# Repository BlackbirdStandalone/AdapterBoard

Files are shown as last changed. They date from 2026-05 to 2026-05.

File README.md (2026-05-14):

# Honda CBR1100XX Super Blackbird - Wiring harness adapter board

This project incorporates a printed circuit board design that allows you to connect from the OEM Honda CBR1100XX Blackbird wiring harness to your stand-alone ECU of choice.
This adapter board specifically targets the early 2000's model EFI Honda Blackbird.

In my case, it is an Australian 2002 model.

The OEM Keihin ECU contains two groups of 22 connector pins that mate with bikes wiring harness. The harness side contains the two connectors (black and light gray) that the ECU mates with. These 22-pin connectors are proprietary and are located underneath the seat at the rear of the motorcycle.

This PCB design provides a means of conveniently interfacing with the existing 22-pin connector to your specific standalone ECU of choice without having to sever the existing wiring harness.
A custom wiring harness can then be separately built to interface to the stand alone ECU via standard Molex connectors numbered at the top of the board.<br/> The benefit of such an interface board also allows you to revert to the original Keihin ECU if you so wish since it allows the bikes wiring harness to remain undisturbed.</BR>
Note: This will only be the case if the camshaft 3-tooth trigger wheel is also left undisturbed.

Fitment to a motorcycle will require the construction of two PCB's. An example of two completed boards are shown below together with its fitment to the existing wiring harness in place of the Keihin ECU.

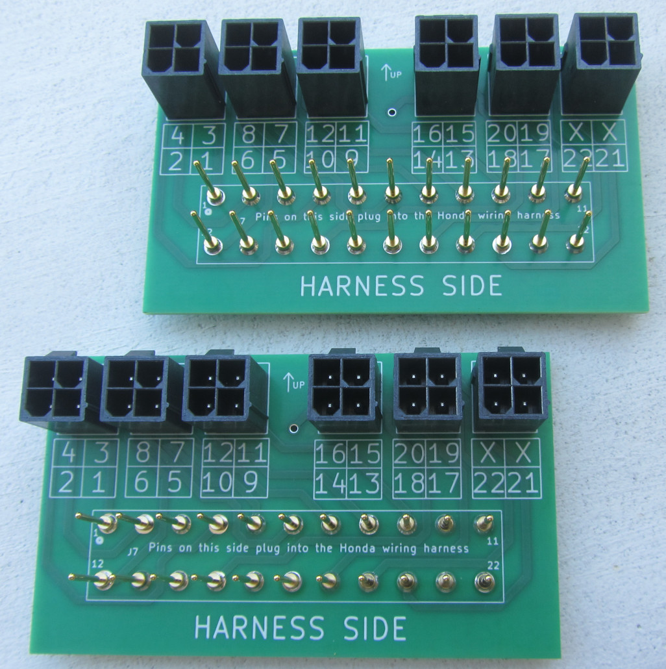
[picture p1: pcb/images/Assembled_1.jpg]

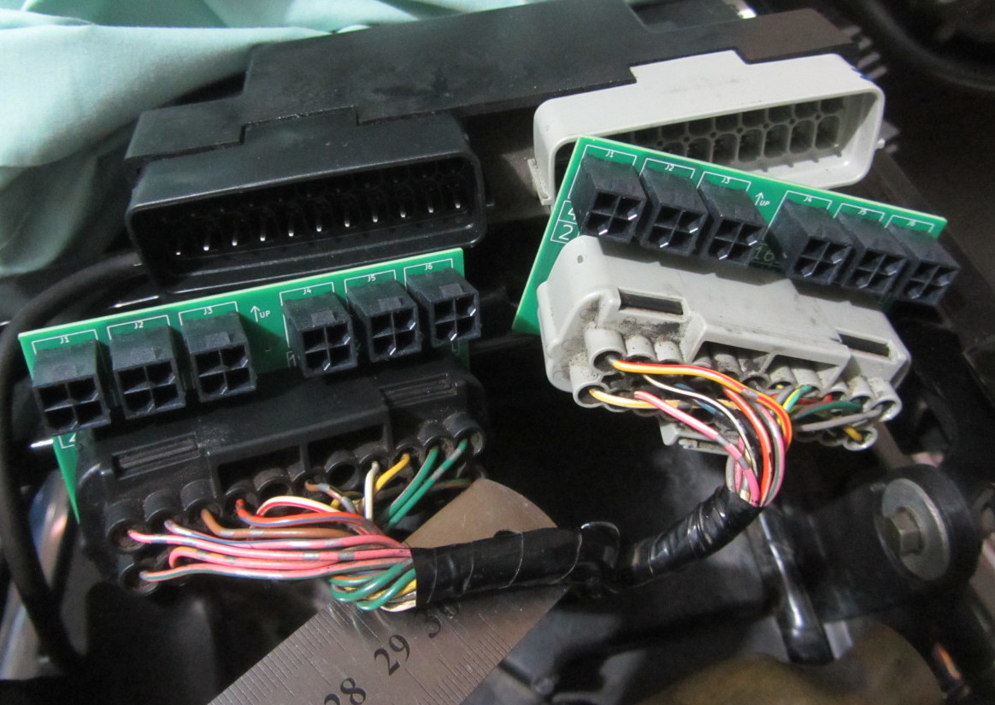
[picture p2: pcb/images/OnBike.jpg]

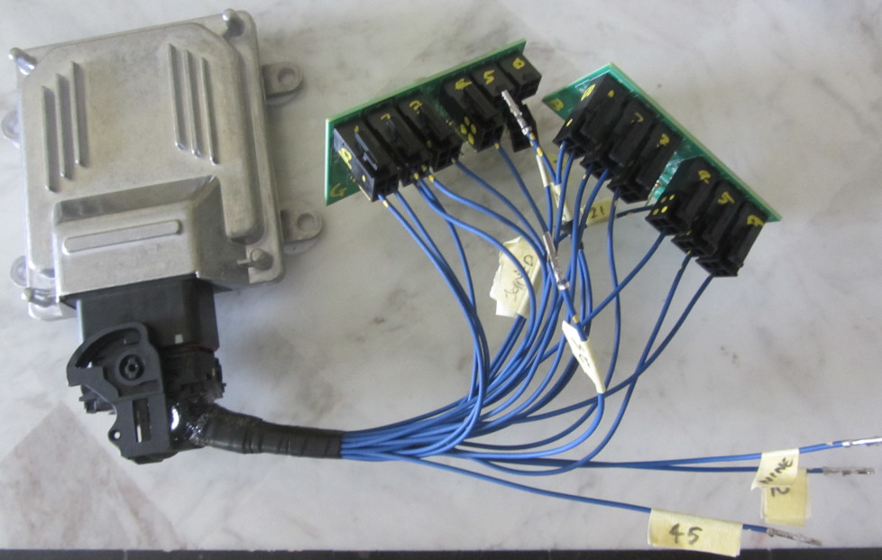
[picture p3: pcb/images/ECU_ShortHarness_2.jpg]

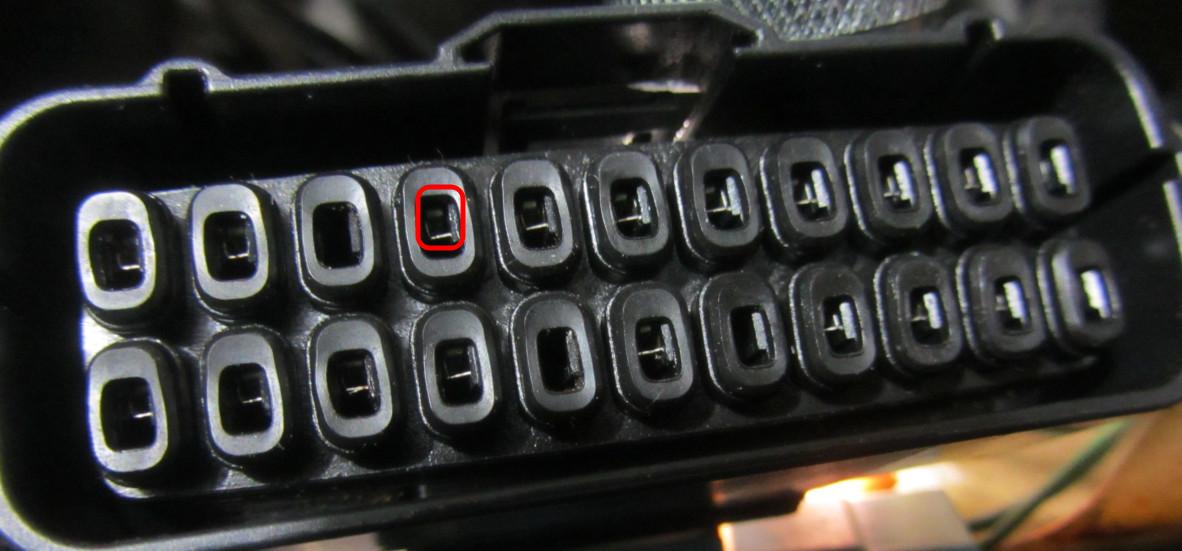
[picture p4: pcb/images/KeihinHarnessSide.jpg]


Note: This project is in its early stages, so does not discuss packaging or sealing of the boards from the elements at this stage. It is evolutionary in nature and will attempt to improve shortcomings over time as new ideas come to light.

</BR>

### Extra Notes
As of this current version (v0.2b), the 22 x round gold-plated pin connectors on the lower half of the board are the closest match I could find as a replacement to the stock Keihin pins.</br>
The stock Keihin pins are 1.0mm wide and 0.7mm tall, therefore a rectangular pin. The replacement I have used is a 1.0mm round style pin. It fits into the harness side very snug. The search for a perfect pin match will continue for future boards revisions.

The last picture displays the Honda/Keihin side of the main bikes wiring harness. It is important that the receptacle (receiver side) is correctly mated with the pins on the PCB since it is easy to mis-align. The area of entry is shown in red. Therefore care must be taken with the pin alignment as the boards are plugged into the black and gray harness side connectors on the bike. The connection will be on the tight side due to the 1.0mm round pins, but they will work.

The pin spacings on the Keihin 22-way connector are 8.5mm in the vertical and 5.8mm horizontally.

The upper half of the board contains a series of 6 x 4-way Molex connectors. The connectors are part of the 'Mini Fit Jnr' family of Molex connectors. The example shown above uses automotive 20 AWG wire. The choice to use many smaller connectors rather than a single 24 way connector was mainly due to stock availability. The 4-way connectors are very common.

</BR>

### Project Details

<table border="1">

<tr> 
<td width="20%">
<strong><u>Current Revision</u></strong>
</td>
<td width="60%">
<strong><u>Date</u></strong>
</td>
<td width="20%">
<strong><u>Author</u></strong>
</td>
</tr>

<tr>
<td width="20%">
v0.2b
</td>
<td width="60%">
May 2026
</td>
<td width="20%">
Alex Kiaos
</td>
</tr>

</table>

</BR>

This project has been designed in Kicad 6.0.11 under linux and is licenced under the CERN Open Hardware Licence Version 2 - Strongly Reciprocal (CERN-OHL-S).</br></br>

The directory structure of this project is as follows:

<p id=directories>
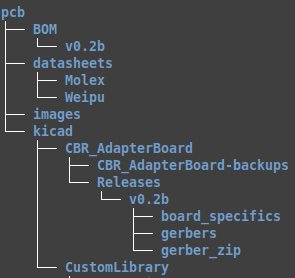
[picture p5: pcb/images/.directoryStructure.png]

</p>

<table border="1">

<tr> 
<td width="20%">
<strong><u>Directory</u></strong>
</td>
<td width="80%">
<strong><u>Description</u></strong>
</td>

</tr>

<tr>
<td width="20%">
BOM
</td>
<td width="80%">
Bill of materials
</td>
</tr>

<tr>
<td width="20%">
datasheets
</td>
<td width="80%">
Data sheets for pins and connectors
</td>
</tr>

<tr>
<td width="20%">
images
</td>
<td width="80%">
Various images, pictures, board renditions
</td>
</tr>

<tr>
<td width="20%">
kicad
</td>
<td width="80%">
The main kicad project folder.<br>
This contains the project itself (uses kicad 6.0.11)</br>
The main project file is 'CBR_AdapterBoard.kicad_pro' found under</br>'/pcb/kicad/CBR_AdapterBoard'.</br></br>
Gerber files can be found as a group of 9 individual files under the 'gerbers' folder or as a single zipped file under the 'gerber_zipped' folder for uploading to a PCB house for manufacture.</br></br>
The 'CustomLibrary' folder contains the custom symbols and footprints used in the project.
</td>

</table>

</br>

After cloning the repository and opening the project for the first time, you may need to set up the symbol and footprint library paths.

To setup the symbols library, in the menu:<br>
<pre><i>Preferences -> Manage Symbol Libraries</i><br>
  Then in the 2nd tab under 'Project specific libraries' add the following:<br>
Nickname: <b>Blackbird</b><br>
Library Path: <b>${KIPRJMOD}/../CustomLibrary/symbols/Blackbird_symbols.kicad_sym</b><br>
</pre>
<br><br>

To setup the footprint library, in the menu:<br>
<pre><i>Preferences -> Manage Footprint Libraries</i><br>
  Then in the 2nd tab under 'Project specific libraries' add the following<br>
Nickname: <b>Blackbird</b><br>
Library Path: <b>${KIPRJMOD}/../CustomLibrary/footprints/</b><br>
</pre>
<br>

# Relevant links

### PCBWay
To visit the PCBWay project and/or place an [order](https://www.pcbway.com/project/shareproject/Honda_CBR1100XX_Super_Blackbird_ECU_adapter_board_for_a_standalone_ECU_a730cd35.html).

### Wiring Harness & Pinouts
To see the ECU pin-out details, refer to the latest pdf file at:
[Wiring Harness Pinout diagram](https://github.com/BlackbirdStandalone/Documentation/tree/main/wiring).

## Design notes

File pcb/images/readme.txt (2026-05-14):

This folder contains various pictures & board renditions related to this adapter board.

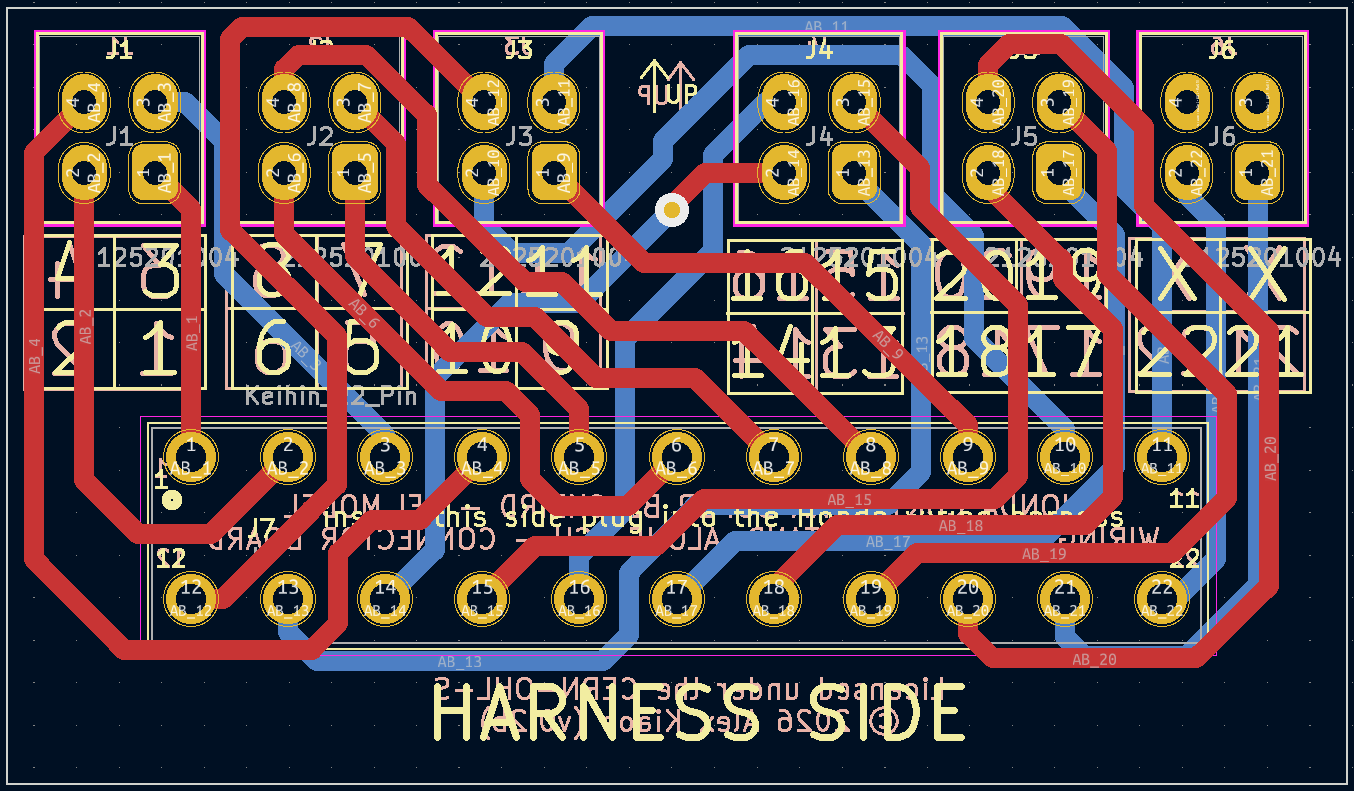
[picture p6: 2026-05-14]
pcb/kicad/CBR_AdapterBoard/Releases/v0.2b/board_specifics/PcbLayout.png

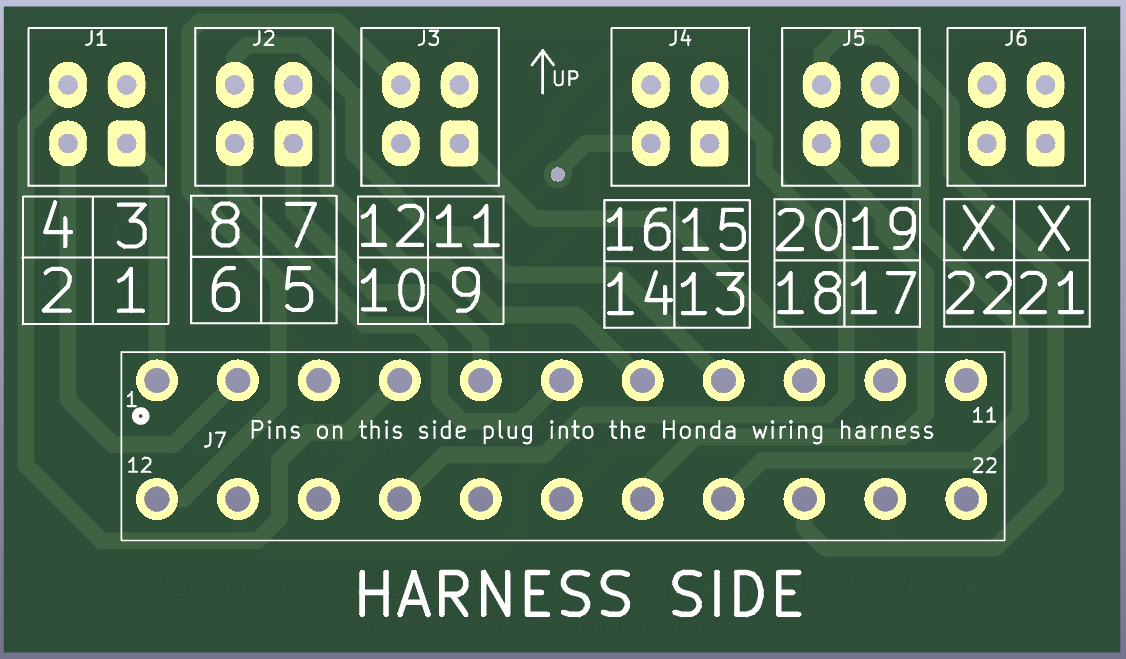
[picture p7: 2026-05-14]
pcb/kicad/CBR_AdapterBoard/Releases/v0.2b/board_specifics/TopSide.png

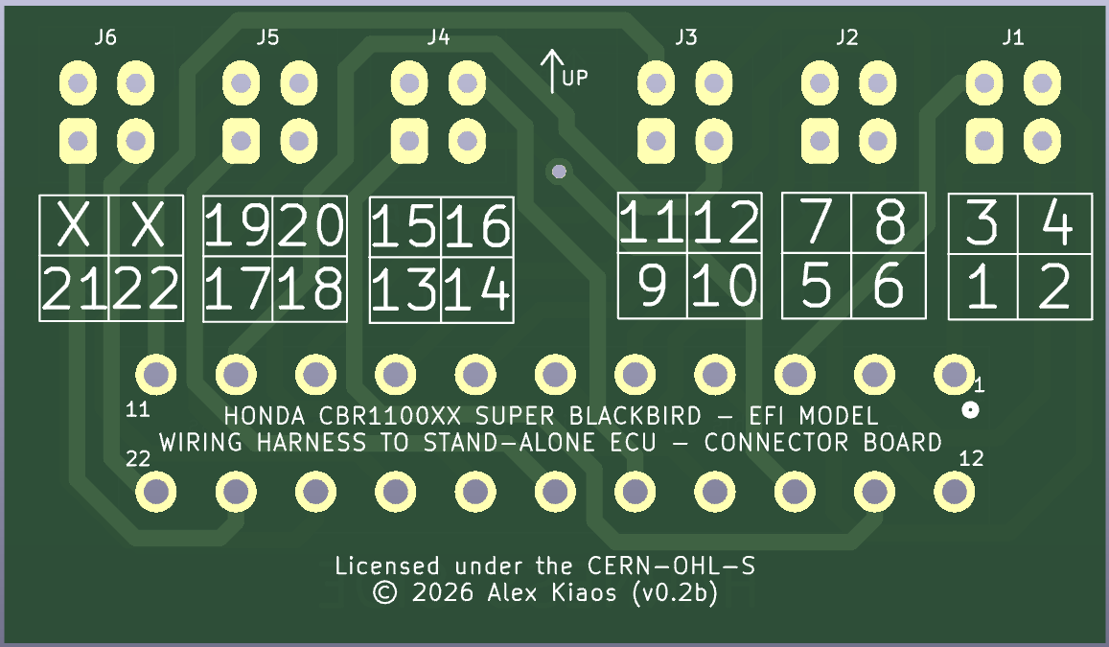
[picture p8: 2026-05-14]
pcb/kicad/CBR_AdapterBoard/Releases/v0.2b/board_specifics/BottomSide.png

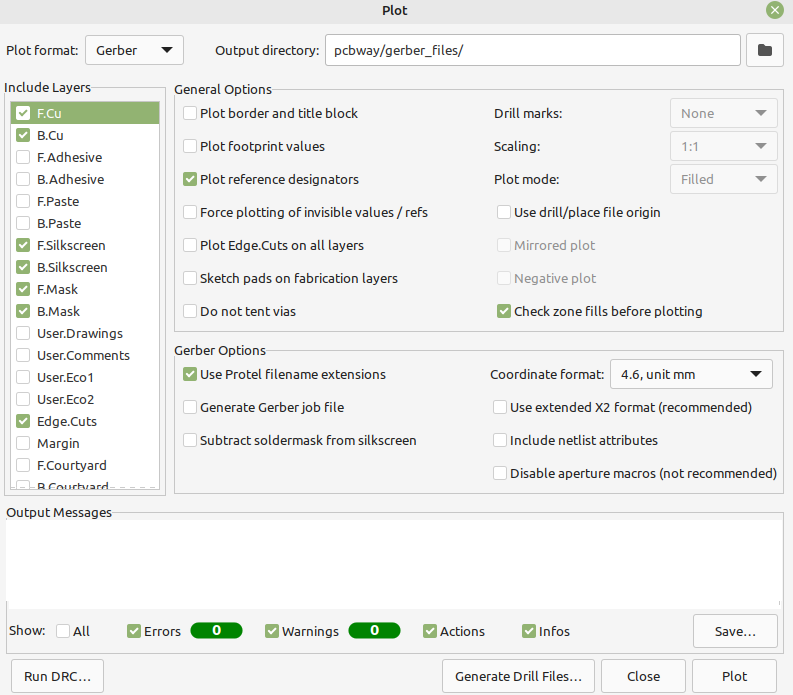
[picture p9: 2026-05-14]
pcb/kicad/CBR_AdapterBoard/Releases/v0.2b/board_specifics/Pcbway_gerber_config.png

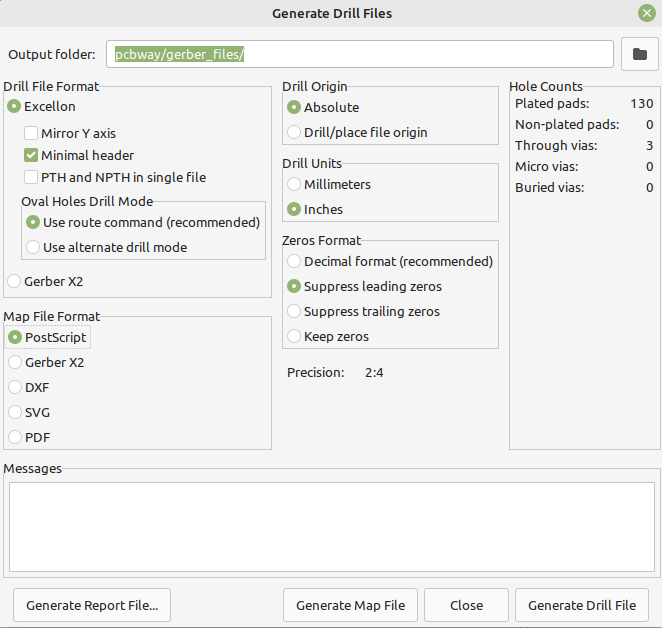
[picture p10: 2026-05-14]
pcb/kicad/CBR_AdapterBoard/Releases/v0.2b/board_specifics/Pcbway_drill_config.png

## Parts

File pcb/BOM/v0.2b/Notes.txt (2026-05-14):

BILL OF MATERIALS (BOM)
----------------------

For one motorcycle, you will need the following parts:

- 2 x PCB boards

- 12 x 4 way Molex connectors (Plug) - Digikey part No: 0462071004-ND
- 12 x 4 way Molex connectors (Receptacle) - Digikey part No: WM13487-ND

- 44 x rectangular connectors - Digikey part No: 0039000038 (order more in case spares are needed)

- 44 x pins - Digikey part No: 5040-YJ1-17-0.52AU-ND (order more in case spares are needed)

Details are outlined in the spreadsheet found in this folder.

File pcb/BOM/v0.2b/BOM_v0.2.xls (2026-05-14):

Category On Board | Board Reference | OEM PART | DigiKey Part No | Series | Description | Link
Pins to Honda harness | J7 | YJ1-17-0.52AU | 5040-YJ1-17-0.52AU-ND | - | Pin Contact 20-24 AWG Size 1.0mm Crimp Gold | https://mm.digikey.com/Volume0/opasdata/d220001/medias/docus/8456/Crimp%20contact%20and%20tool.pdf
PLUG (Molex) | J1-J6 | 462071004 (MOLEX) | 0462071004-ND | Mini-Fit Jr. 46207 Series | CONN HEADER VERT 4POS 4.2MM | https://www.digikey.com.au/en/products/detail/molex/0462071004/3311552
PLUG (Receptacle) | J1-J6 | 39013045 (MOLEX) | WM13487-ND | 5557 | CONN RCPT HSG 4POS 4.20MM | https://www.digikey.com.au/en/products/detail/molex/0039013045/3160117
WIRING - (Wire to receptacle) | J1-J6 | 39000038 (MOLEX) | WM2501TR-ND or WM2501CT-ND | Mini-Fit Jr 5556 | CONN SOCKET 18-24AWG CRIMP TIN | https://www.digikey.com.au/en/products/detail/molex/0039000038/413211
(alternate) WIRING - (Wire to receptacle) |  | 39000073 (MOLEX) | WM6890TR-ND or WM6890CT-ND | Mini-Fit Jr 5556 | CONN SOCKET 18-24AWG CRIMP GOLD | https://www.digikey.com.au/en/products/detail/molex/0039000073/3044236
Notes
TO ORDER IN GREEN

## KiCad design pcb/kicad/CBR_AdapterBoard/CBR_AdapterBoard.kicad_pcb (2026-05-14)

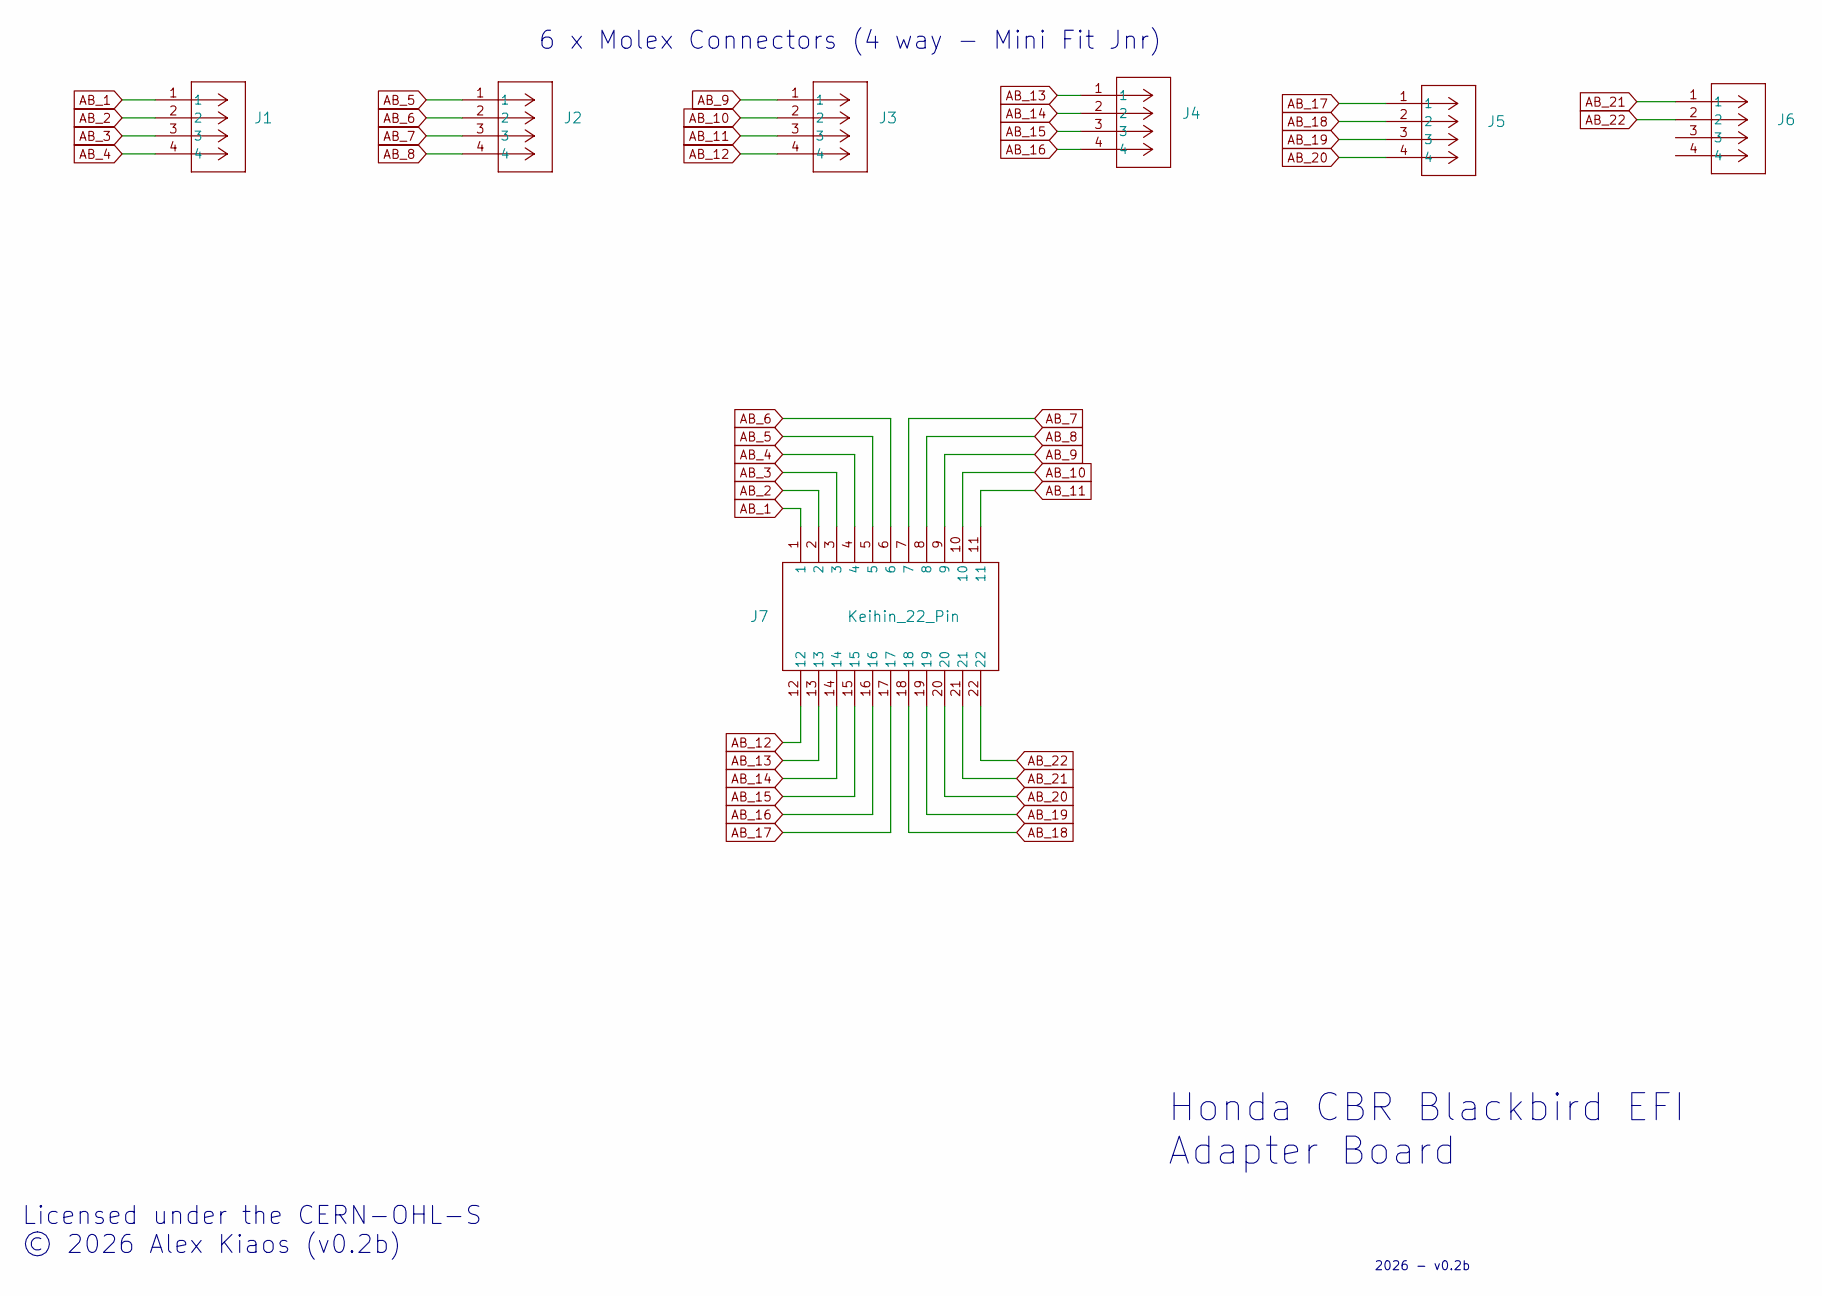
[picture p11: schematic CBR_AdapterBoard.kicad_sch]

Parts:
J1, J2, J3, J4, J5, J6: 2125201004; 4-Way-Molex_Connector-MiniFit-JNR
J7: Keihin_22_Pin; Blackbird_22_pin_keihin

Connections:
AB_1: J1.1, J7.1
AB_2: J1.2, J7.2
AB_3: J1.3, J7.3
AB_4: J1.4, J7.4
AB_5: J2.1, J7.5
AB_6: J2.2, J7.6
AB_7: J2.3, J7.7
AB_8: J2.4, J7.8
AB_9: J3.1, J7.9
AB_10: J3.2, J7.10
AB_11: J3.3, J7.11
AB_12: J3.4, J7.12
AB_13: J4.1, J7.13
AB_14: J4.2, J7.14
AB_15: J4.3, J7.15
AB_16: J4.4, J7.16
AB_17: J5.1, J7.17
AB_18: J5.2, J7.18
AB_19: J5.3, J7.19
AB_20: J5.4, J7.20
AB_21: J6.1, J7.21
AB_22: J6.2, J7.22

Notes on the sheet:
Honda CBR Blackbird EFI Adapter Board
6 x Molex Connectors (4 way - Mini Fit Jnr)
Licensed under the CERN-OHL-S © 2026 Alex Kiaos (v0.2b)
2026 - v0.2b

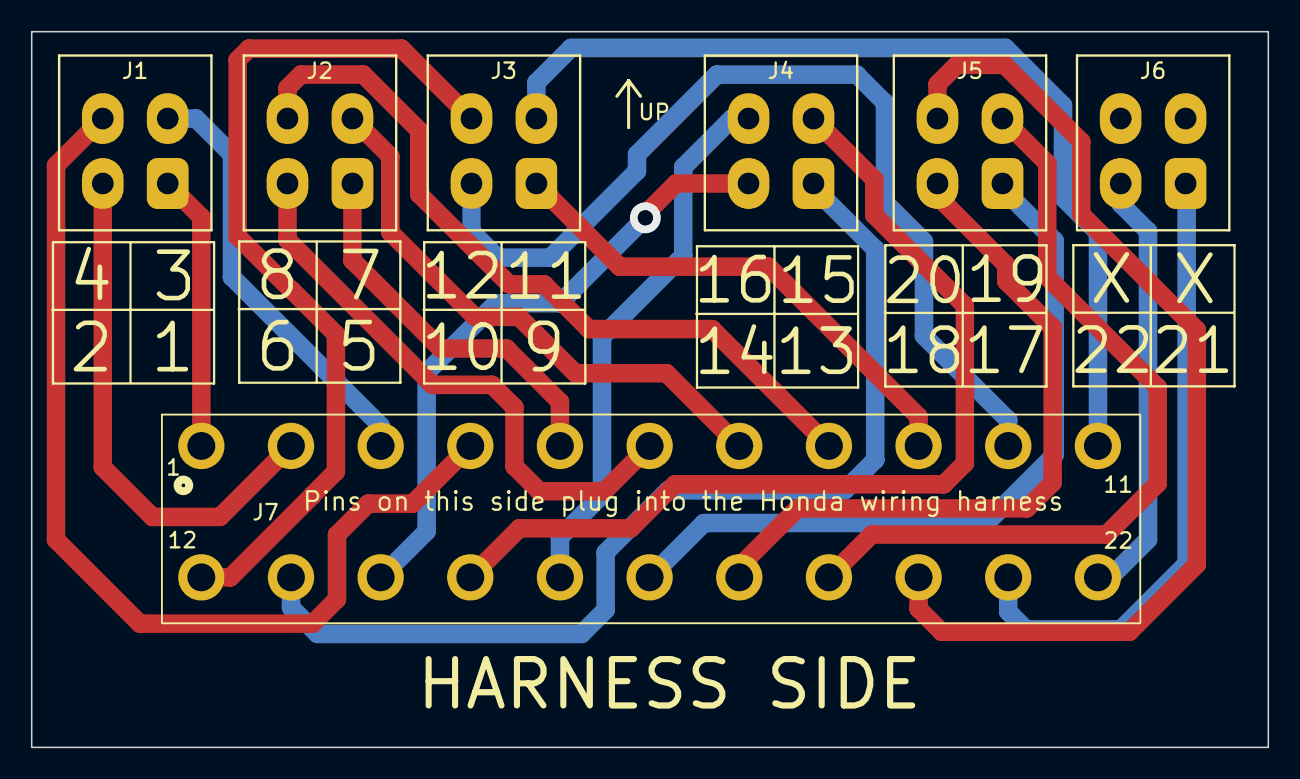
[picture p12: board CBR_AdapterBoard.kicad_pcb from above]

Board: 2 copper layers, 80.0 x 46.3 mm, 7 parts (0 on the bottom side), 22 nets.

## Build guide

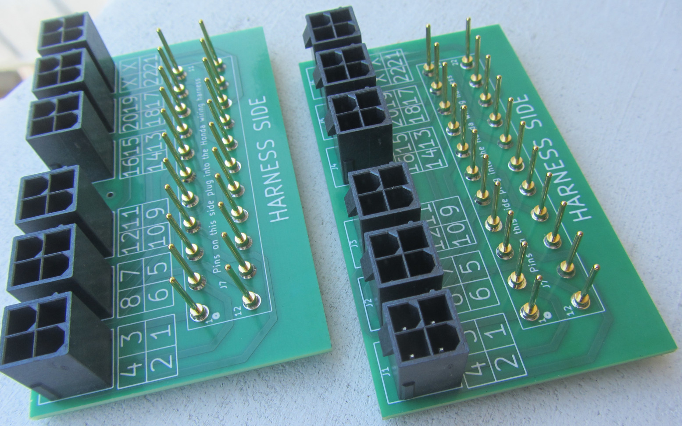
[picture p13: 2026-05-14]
pcb/images/Assembled_2.jpg
